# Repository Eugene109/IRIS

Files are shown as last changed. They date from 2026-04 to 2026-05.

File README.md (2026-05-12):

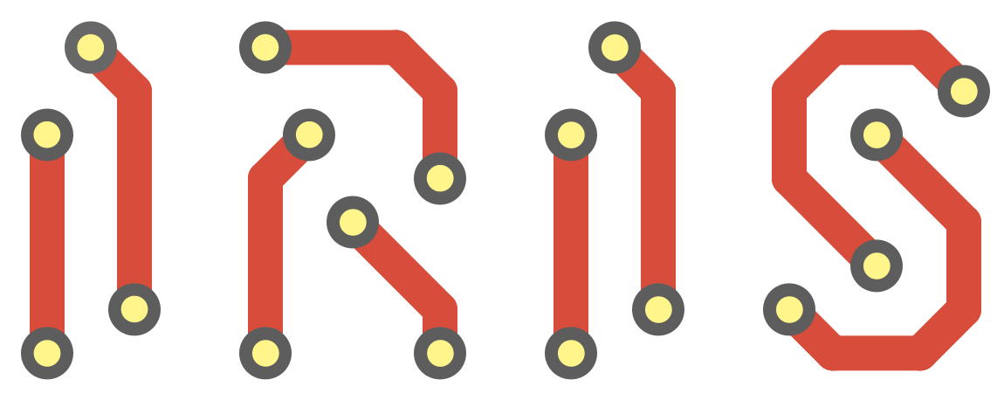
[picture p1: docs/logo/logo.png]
IRIS


> A low-cost quadcopter platform designed for autonomous swarm operations.



Photorealistic render from the back-right-top side of the drone

## Overview
IRIS is centered around a mass-manufacturable low-cost PCB, containing a flight controller and 4 ESCs. Designed with the idea of delivering Skittles autonomously, IRIS is built from the ground-up for autonomous operation in swarms. With a rich sensor set and high degree of customizability, IRIS represents an accessible, low-cost entry into the world of autonomous and swarm drone operations. I began this project because I found a lack of accessible drone designs that are for more than just 'fun FPV flying', and I wanted to be able to program a drone to do cool things. IRIS represents a rethinking of small drone design, believing that small drones can and should be autonomous and that everyone should be able to program a drone.
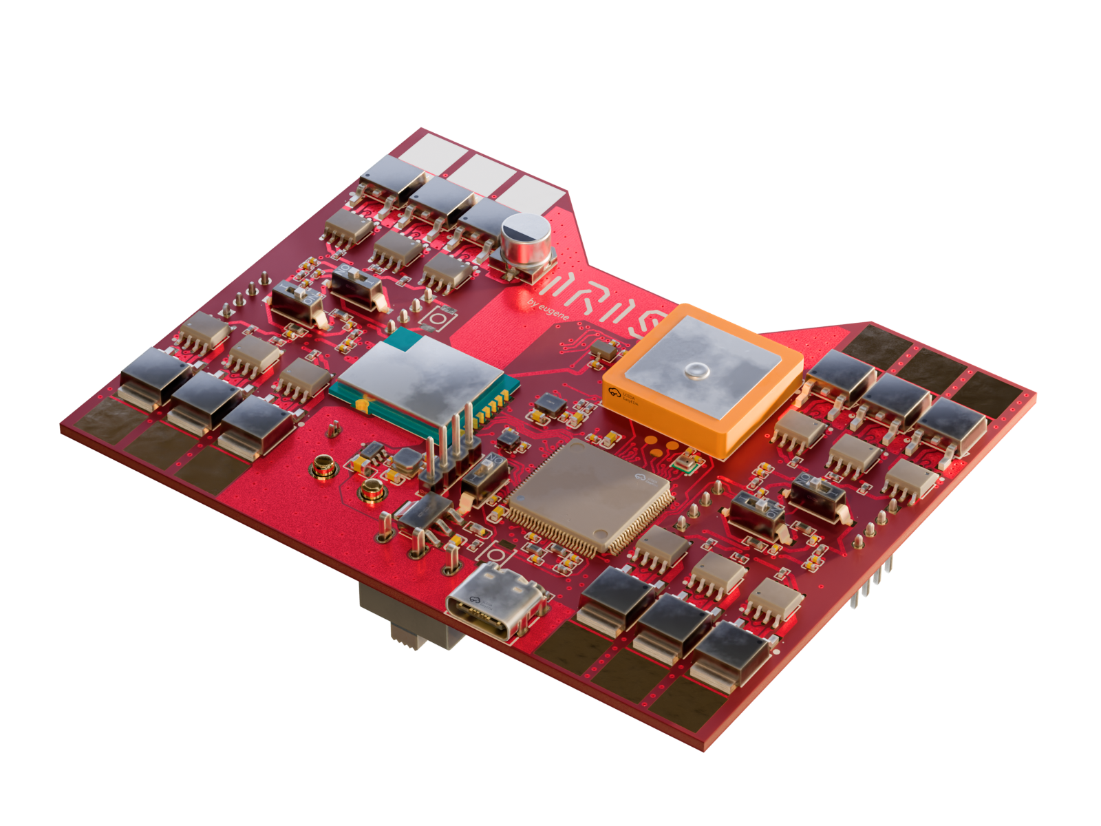
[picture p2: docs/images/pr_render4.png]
Photorealistic render of the front side of the PCB


## Features
 - STM32H743 MCU
 - IMU, Barometer, Magnetometer, GPS
 - Integrated 4-in-1 ESC with sensorless drive
 - OV2640 camera for computer vision
 - 2.4GHz Radio Transciever + nanoELRS header
 - 2S LiPo input, XT60 connector
 - 3D-printed frame

## Table of Contents
- [Design Features](#design-features)
  - [Flight Controller Design](#flight-controller-design)
  - [ESC Design](#esc-design)
  - [Frame Design](#frame-design)
- [Getting Started](#getting-started)
- [PCB Assembly](#pcb-assembly)
- [Bill of Materials](#bill-of-materials)
- [Drone Assembly](#drone-assembly)
- [Firmware](#firmware)
- [Roadmap](#roadmap)

## Hack Club Magazine Page
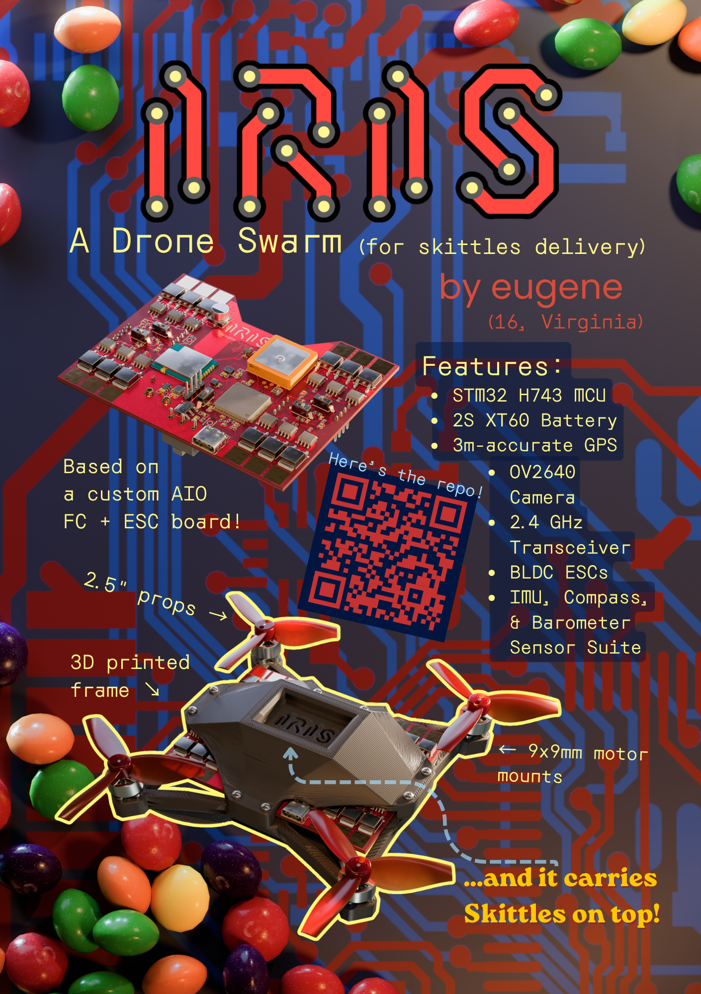
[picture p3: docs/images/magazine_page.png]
A5 magazine page


## Design Features

### Flight Controller Design
<p align="center">
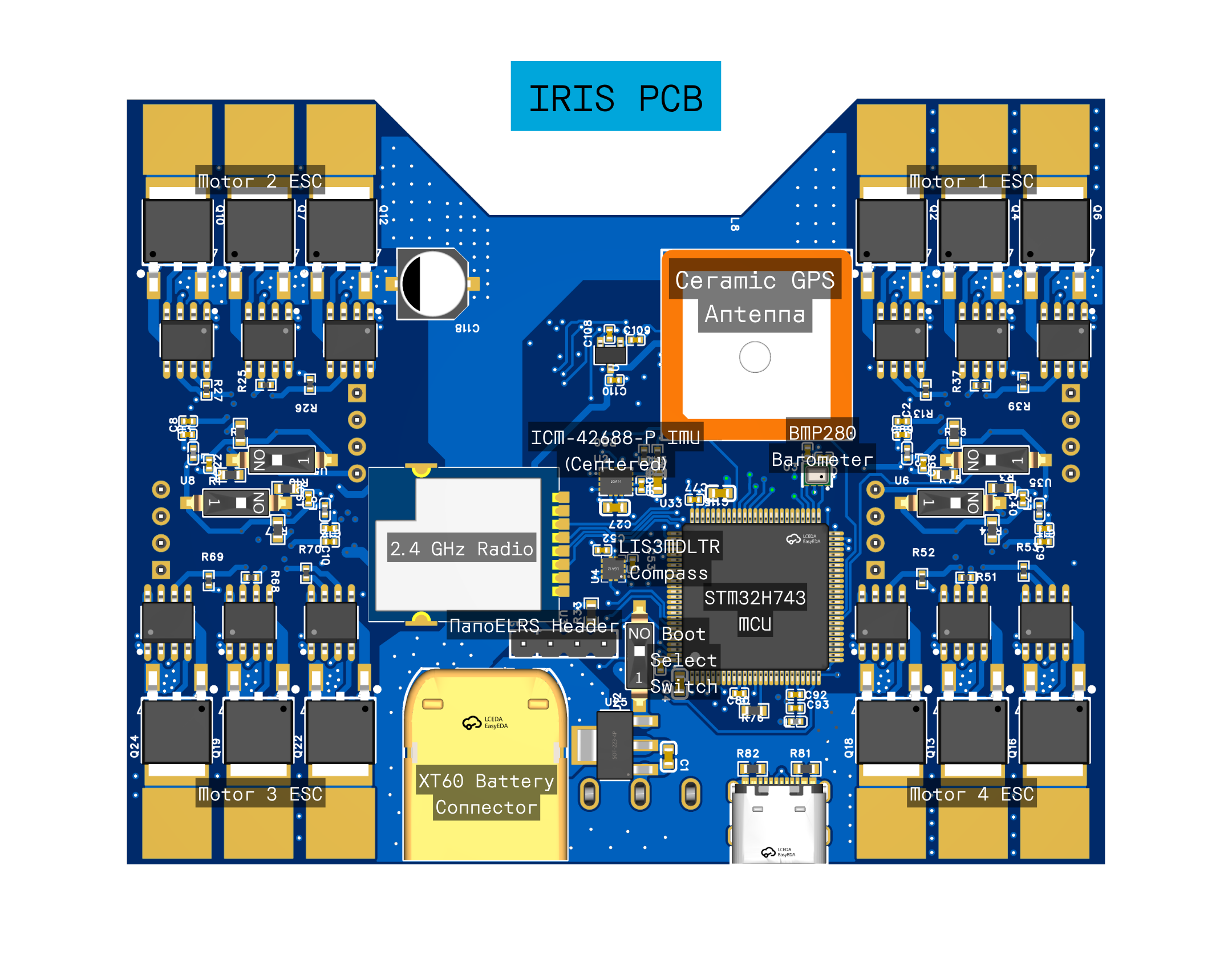
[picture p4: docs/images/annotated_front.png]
Annotated render of the front of the PCB
  
&nbsp; &nbsp; &nbsp; &nbsp;
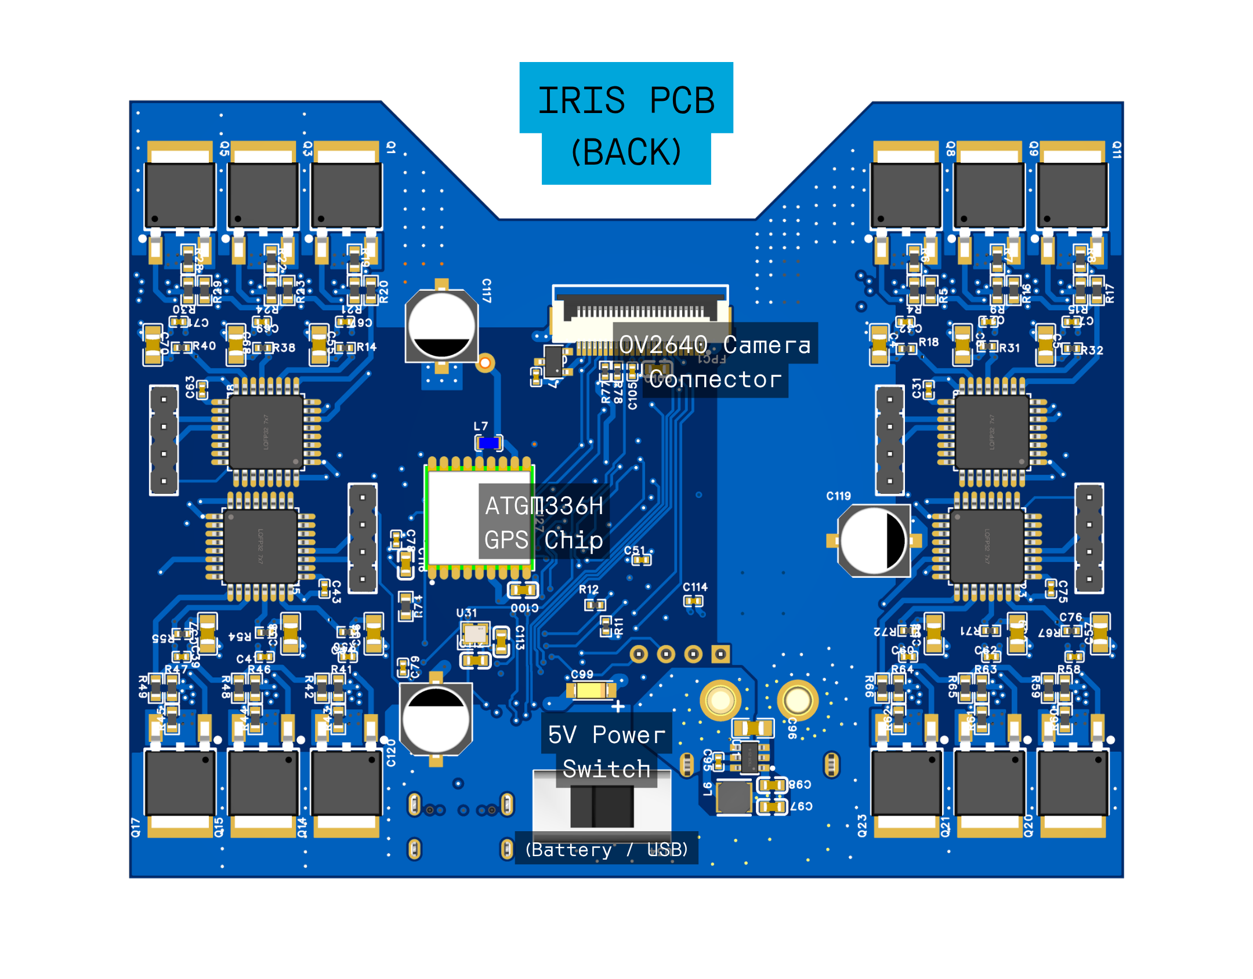
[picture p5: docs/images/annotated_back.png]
Annotated render of the back of the PCB
  
</p>

[Schematic](./pcb/schematics/Flight_Controller_Schematic.svg)

The PCB design features a 4-layer PCB stackup for lowered manufacturing costs, with a (nearly) continuous ground plane for reduced RF interference. The area under the MCU and core sensors also feature a continuous 3.3V power plane. The high voltage and current for the ESCs are routed on large copper pours on the bottom layer, with cross-layer connections connected by suture vias.

The total board dimensions are 3.650" by 2.856", a little larger than a credit card.

The main flight controller MCU is programmable over USB. The 4 ESC MCUs require a serial programmer, with ground, rx and tx exposed on header pins. All MCUs have a dedicated switch for a physical boot selector.

### ESC Design

[Schematic](./pcb/schematics/ESC_Schematics/Motor1_ESC_Schematic.svg)

The ESC design features an STM32F303K8T6 microcontroller, a very powerful MCU that enables accurate back-emf drive even for high kV motors. 

Loosely based off of this open-source design I found,
https://electronoobs.com/eng_arduino_tut91.php, the wiring diagram was very helpful to guide the general layout of my ESC. The control logic is loosely based off of the arduino code, though it had to be completely rewritten to interface with STM32 hardware (really all BLDC motor control logic is the same, but nice understandable code was helpful).

### Frame Design
The frame design merges swooping curves and sharp geometric angles in a retrofuturistic visual style. Inspired by the Theme Building at LAX, the frame arms are each constructed with 3 catenary curves, with the bottom arches merging together to form the cradle for the battery.

The bottom also features a -30º camera mount, which facilitates autonomous navigation, and turns into the perfect FPV mount when flown inverted.
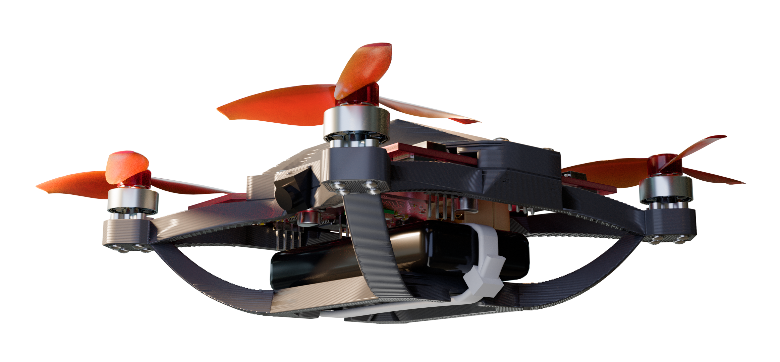
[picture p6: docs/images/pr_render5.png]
Photorealistic render from the back-left side of the drone


At the top of the frame, a little cradle with a minimalist IRIS logo debossed reserves space for a small collection of Skittles, easily dumped out by flipping the drone.

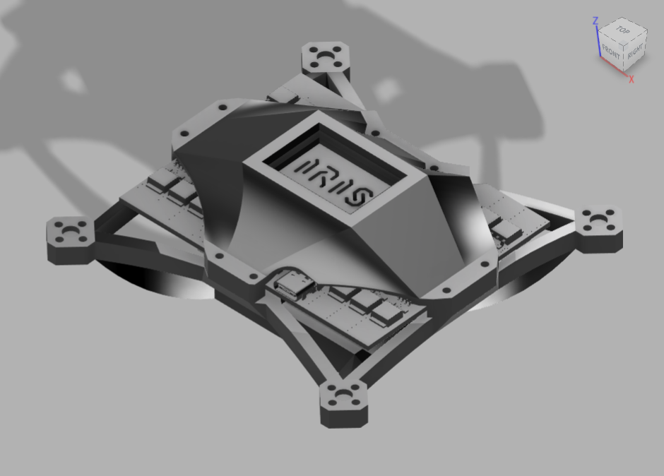
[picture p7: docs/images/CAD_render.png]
CAD render of the integrated frame + PCB


The drone frame is constructed in two pieces and held together by 8 M2 screws. The bottom half contains a battery mount and 4 9x9mm motor mounts, while the top half clamps the PCB down. The top cover shields the bulk of the PCB while leaving the high-current ESC MOSFET sections exposed for cooling, and is bolted down using 8 10mm long M2 screws and heat set inserts on the bottom half.

## Getting Started

### Prerequisites

- EasyEDA Pro (recommended)
- KiCAD 10.0 (broken DRC rules)
- Fusion 360
- Blender 5.0+ ([pcb2blender](https://github.com/30350n/pcb2blender) extension required for textures)

### For KiCAD Users:
This project was made in the free software EasyEDA Pro, and the design is native to that software. The PCB design has been converted to a KiCAD project for easier access to the design, but there may be some errors that have occurred during the import process, in particular trace clearances and zone fill rules.

> NOTE: The KiCAD imported project relies on 3D models and footprints from LCSC, which were imported using [easyeda2kicad.py](https://github.com/uPesy/easyeda2kicad.py).

### Repository Structure
All of the files for the flight controller + ESC board are contained in `pcb/`, with fabrication files in `pcb/fabrication/`. All fabrication files are to [JLCPCB](https://jlcpcb.com/) specifications. All part numbers are from [LCSC](https://www.lcsc.com/).

The frame CAD files can be found in the `frame/` directory, with (metric) STL and 3MF exports ready for 3D printing. The cover and bottom were designed in the same Fusion360 Part, and the IRIS_Assembly.f3z is the total assembly including parts I did not design.

All of the renders on the documentation were created using Blender 5.1, and render files can be found in `docs/render/`.

## PCB Assembly

### PCB Component Bill of Materials
[PCB Component BOM](./pcb/fabrication/BOM.md)

Total cost from LCSC: **$103.21**
[LCSC Quote](./pcb/fabrication/LCSC_BOM_export.xls)

### Assembly

The [PCB gerbers](./pcb/fabrication/gerbers.zip) can be manufactured by JLCPCB with the simple 4-layer PCBA economical service. Two-sided automated assembly is quite expensive however, so first prototypes will be assembled manually using solder stencils. PCB components can be ordered from LCSC using the [LCSC BOM](./pcb/fabrication/BOM_Board1_PCB1.xlsx).
> NOTE: The large copper pours are connected directly to a lot of the pads, manual soldering will require the use of a hot air rework station and powerful soldering iron

## Bill of Materials
> Note: the full list of components for the PCB was not included in this BOM to save space, the component BOM can be found [here](./pcb/fabrication/BOM.md)

| Part | Description | Link | Price |
| --- | --- | --- | ----- |
| FC+ESC | 4-layer PCB A Economic, HASL(leaded) finish, 2 stencils w/ framework | [JLCPCB](https://cart.jlcpcb.com/quote) (Please upload ./pcb/fabrication/gerbers.zip to order the PCB) | 29.23 |
| FC+ESC | IRIS PCB Components | [LCSC](https://www.lcsc.com/) (Please upload ./pcb/fabrication/BOM_Board1_PCB1.xlsx to order the components) | 103.21 |
| Battery | 1000 mAh 2S LiPo with XT60 connector| [Admiral](https://motionrc.com/products/admiral-1000mah-2s-7-4v-30c-lipo-battery-with-xt60-connector-epr10002x6) | 9.99 |
| Motors | 4x 8000 kV 1103 Brushless DC | [AliExpress](https://www.aliexpress.us/item/3256808118156099.html) | 23.99 |
| Propellers | Gemfan 2512 2.5Inch 3-Blade 1.5mm Hole Propeller - 4CW+4CCW | [Pyrodrone](https://pyrodrone.com/products/gemfan-2512-2-5inch-3-blade-1-5mm-2mm-hole-propeller-4cw-4ccw) | 4.99 |
| Camera | OV2640 with SCCB cable | [AliExpress](https://www.aliexpress.us/item/3256805331385102.html) | 4.20 |
| Heat-set inserts | M2x2.5mm, 3.5mm OD Knurled Brass Threaded Heat Set Inserts | [Rusty Bolt Shop](https://ebay.us/m/7A3cL3) | 1.70 |
| Frame screws | M2x10mm screws | [The Rusty Bolt Shop](https://ebay.us/m/wMPMiQ) | 2.02 |
| Motor mount screws | M2x8mm screws | [The Rusty Bolt Shop](https://ebay.us/m/UnEsMj) | 2.56 |
| Vibration dampening foam | 3M Double Coated Urethane Foam Tape 4056 | [Newegg](https://www.newegg.com/p/2VW-0006-00155?item=9SIA5D52U89288) | 14.99 |

Total: $196.88
(minus shipping)

## Drone Assembly
1. Print the frame in two sections
2. Attach heat-set inserts with a soldering iron on the base half of the frame.
3. Cut 4056 foam to shape and attach to the PCB contact areas on both sides of the frame.
4. Attach the OV2640 camera SCCB cable to the connector and attach 4056 foam to the back of the sensor.
5. Insert the assembled PCB between the two frame sections and bolt down all 8 M2x10mm screws.
6. Slot the camera sensor into its 30º mount and attach using 4056 foam.
7. Insert the battery into the cradle underneath the PCB, mount it with 4056 foam and fasten down with zip ties across the horizontal beams, inside of the grooves.
8. Attach brushless motors with M2x8mm screws.
9. Press-fit 2CCW and 2CW propellers onto the four brushless motors' 1.5mm shafts.
10. Flash the [Betaflight firmware](./firmware/betaflight/binaries/betaflight_2026.6.0-alpha_STM32H743_IRIS_H743.hex) using a USB-C cable.
11. Flash the [Zephyrus firmware](https://github.com/Eugene109/zephyrus/releases/latest) to all four ESCs using a serial programmer attached to the 4-pin headers.
11. Fly!

## Firmware
### Betaflight
This flight controller is capable of running Betaflight, and the configuration header for a Betaflight target can be found in `firmware/betaflight/`. The compiled binaries can be found in the same directory, and the `.hex` file is recommended. The source code can be found at the [Betaflight firmware repository](https://github.com/betaflight/betaflight), and the `config.h` file can be copied into the config directory to build it yourself.

The flight control software can be flashed using the USB-C port on the aft of the drone. Simply plug it in and use STMCubeProgrammer to flash it!

### Zephyrus
The ESCs run custom firmware, named Zephyrus. The binaries and source code is available at its [repository](https://github.com/Eugene109/zephyrus).

Zephyrus is currently capable of sensorless back-EMF drive, and runs on the STM32F303K8T6 MCU platform. The sensorless drive is powered by ADC zero-crossing detection synchronized with the PWM output to the MOSFET drivers. The choice to use software detection of zero-crossing over hardware comparators was for the increased flexibility as the firmware matures, enabling more interesting control systems than just zero-crossing alone.

The ESCs are a bit harder to flash, though they should require only a single flashing when the firmware is tuned. Connect a serial programmer (FTDI, hijack an Arduino, etc) to the RX, TX, and GND pins and flash the MCU using the ROM bootloader. To switch the MCU to the built-in bootloader to program, simply flip the boot selector switch and press the reset button.

## Roadmap

- [X] PCB designed
- [X] Case designed
- [ ] PCB assembled
- [ ] Prototype assembled
- [ ] Prototype tested
- [ ] Firmware finalized
- [ ] PCB mass-produced

## License

Everything is [GNU GPL-3.0](LICENSE)

zephyrus firmware is licensed under MIT, check its [repo](https://github.com/Eugene109/zephyrus) for more information.

> **Trademark Notice:** Skittles® is a registered trademark of Mars, Inc. This project is not affiliated with, or sponsored by Mars, Inc. References to Skittles and any associated imagery are for descriptive purposes only.

### Attribution
1103 BLDC motor 3D model used in Fusion Assembly is from [GrabCAD](https://grabcad.com/library/geprc-gr1103-1) by [Dang Ngoc Duy](https://grabcad.com/dang.ngoc.duy-1)

2.5" propeller 3D model used in Fusion Assembly is from [GrabCAD](https://www.thingiverse.com/thing:6901068) by [Buddhas_Priest](https://www.thingiverse.com/Buddhas_Priest)

rostock_laage_airport_4k.exr is CC0 from PolyHaven, credit to Greg Zaal

Inspiration was taken from [Electronoobs's ESC design], informing the framework for a standard ESC architecture.

None of the PCB 3D models are my own work, they come from LCSC's libraries.

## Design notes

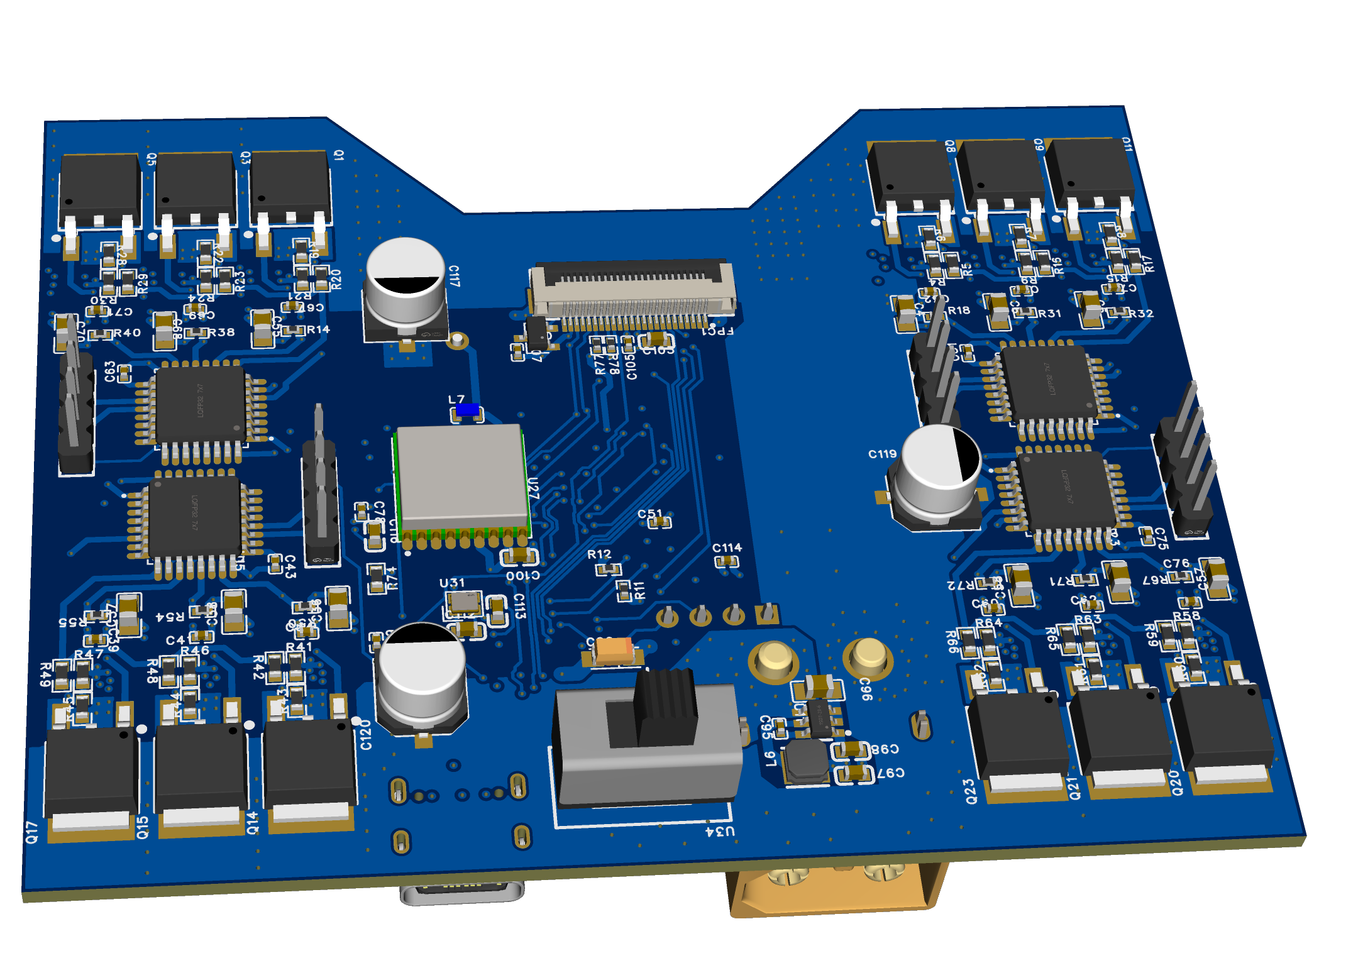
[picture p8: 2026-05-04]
docs/images/PCB_Back_RENDER.png

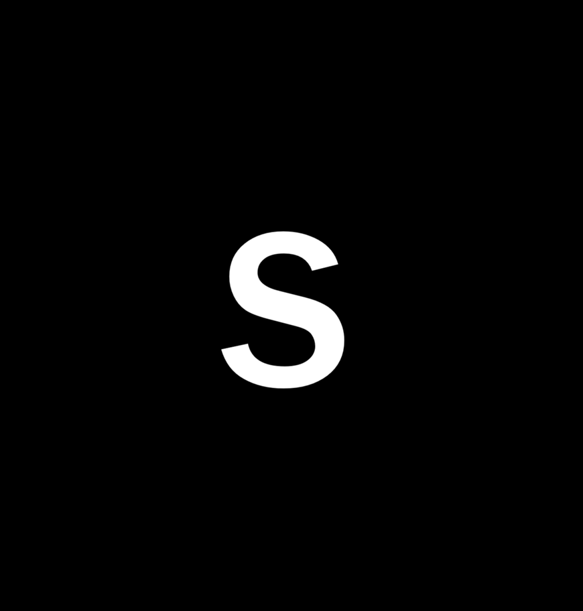
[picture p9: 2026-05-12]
docs/render/s.png

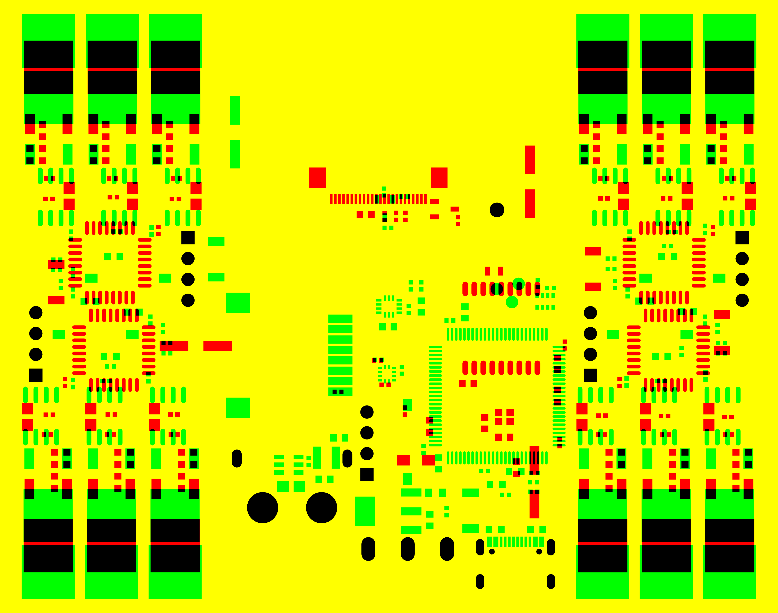
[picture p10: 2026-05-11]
docs/render/textures/IRIS_PCB_model_Mask.png

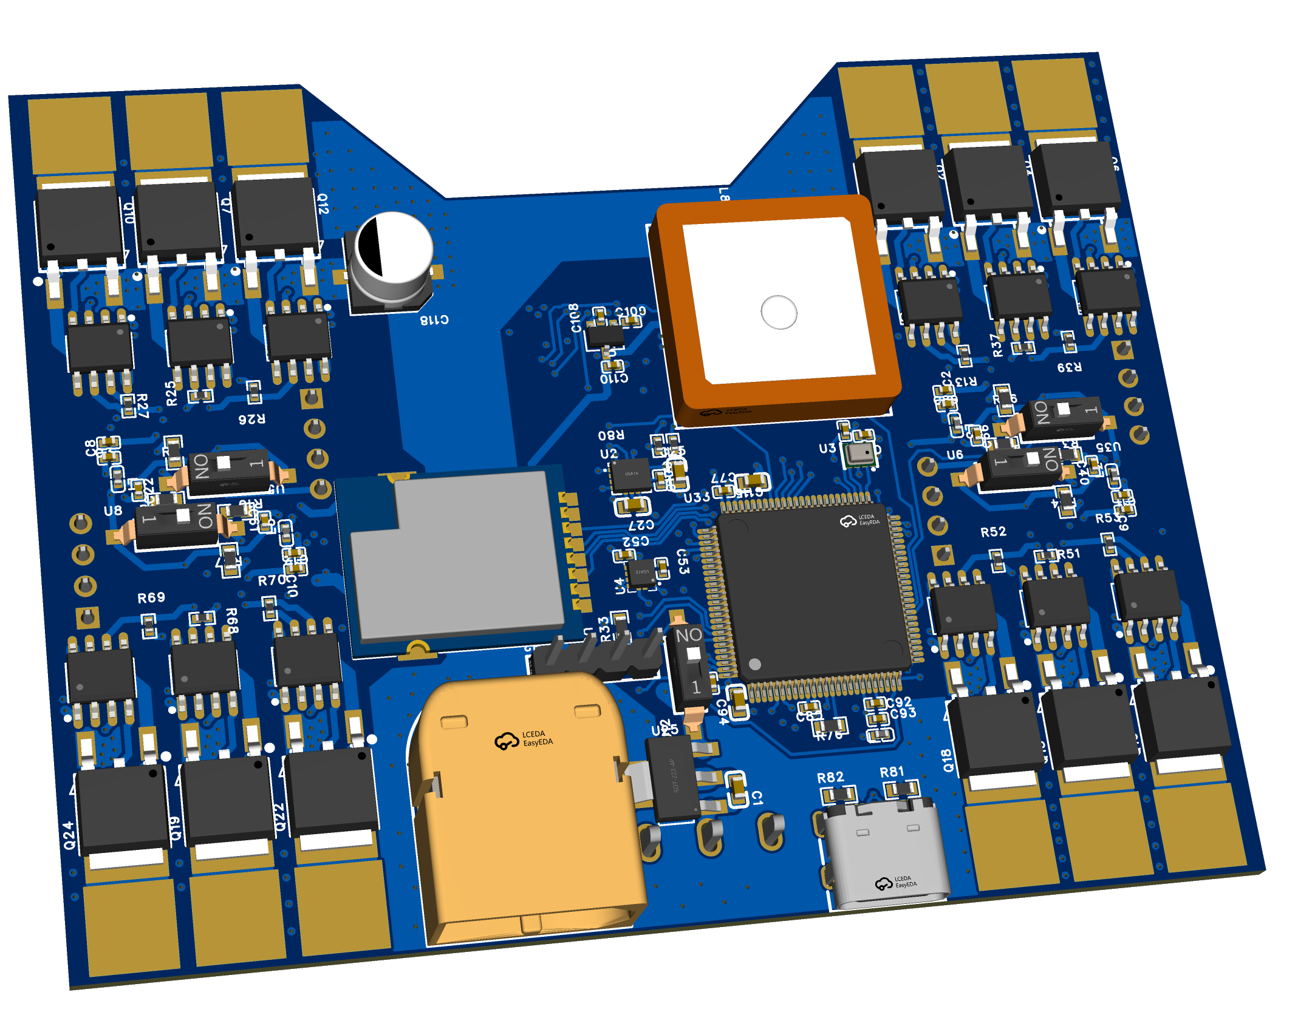
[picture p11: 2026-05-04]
docs/images/PCB_Front_RENDER.png

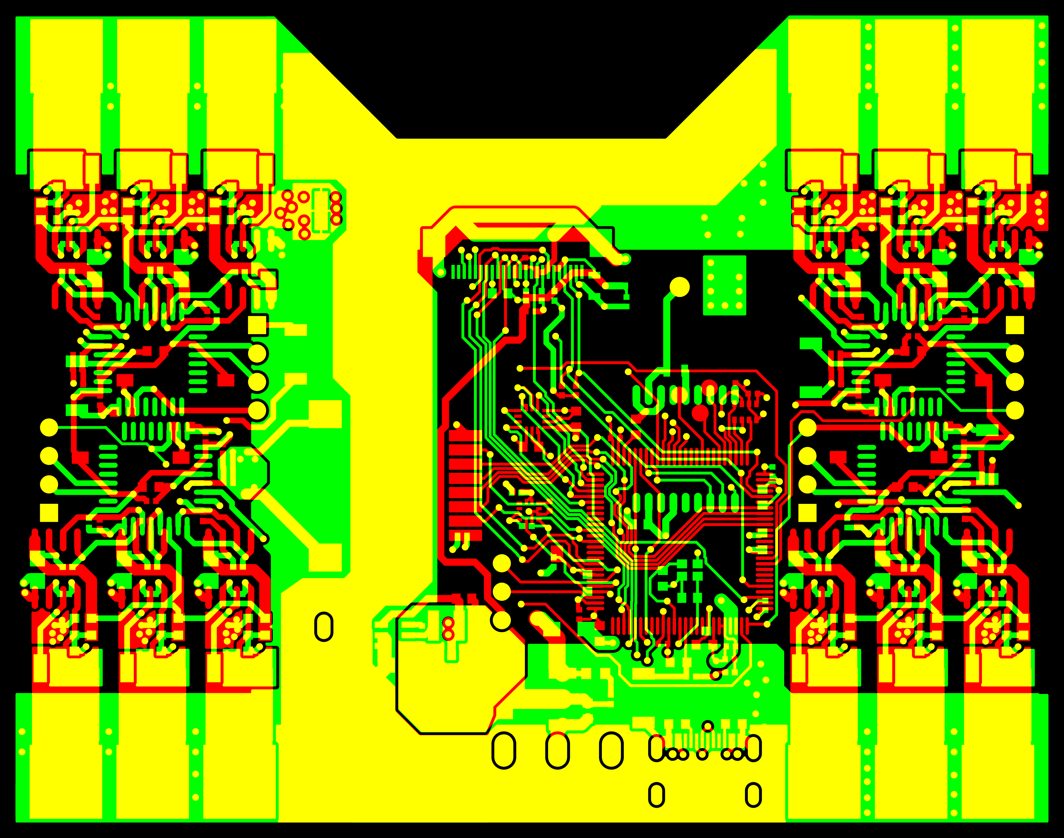
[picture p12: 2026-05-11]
docs/render/textures/IRIS_PCB_model_Cu.png

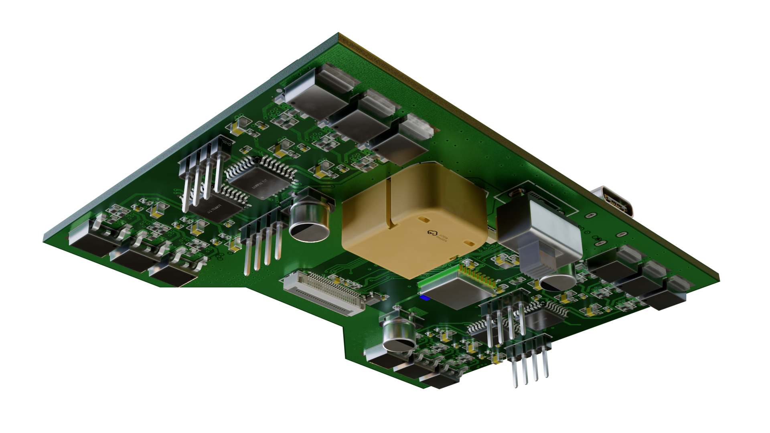
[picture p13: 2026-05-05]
docs/images/pr_render2.png

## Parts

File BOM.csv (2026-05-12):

Quantity | Part | Description | Source | Link | Price
1 | FC+ESC | 4-layer PCB A Economic HASL(leaded) finish 2 stencils w/ framework | JLCPCB | N/A: Please upload pcb/fabrication/gerbers.zip to https://www.jlcpcb.com/ to order | 29.23
1 | FC+ESC | IRIS PCB Components | LCSC | Please upload pcb/fabrication/BOM_Board1_PCB1.xlsx to https://www.lcsc.com/; alternatively see pcb/fabrication/BOM.md for LCSC links | 103.21
1 | Battery | 1000 mAh 2S LiPo with XT60 connector | Admiral | https://motionrc.com/products/admiral-1000mah-2s-7-4v-30c-lipo-battery-with-xt60-connector-epr10002x6 | 9.99
1 | Motors | 4x 8000 kV 1103 Brushless DC | AliExpress | https://www.aliexpress.us/item/3256808118156099.html | 23.99
1 | Propellers | Gemfan 2512 2.5Inch 3-Blade 1.5mm Hole Propeller - 4CW+4CCW | Pyrodrone | https://pyrodrone.com/products/gemfan-2512-2-5inch-3-blade-1-5mm-2mm-hole-propeller-4cw-4ccw | 4.99
1 | Camera | OV2640 with SCCB cable | AliExpress | https://www.aliexpress.us/item/3256805331385102.html | 4.20
1 | Heat-set inserts | M2x2.5mm 3.5mm OD Knurled Brass Threaded Heat Set Inserts | Rusty Bolt Shop | https://ebay.us/m/7A3cL3 | 1.70
1 | Frame screws | M2x10mm screws | The Rusty Bolt Shop | https://ebay.us/m/wMPMiQ | 2.02
1 | Motor mount screws | M2x8mm screws | The Rusty Bolt Shop | https://ebay.us/m/UnEsMj | 2.56
1 | Vibration dampening foam | 3M Double Coated Urethane Foam Tape 4056 | Newegg | https://www.newegg.com/p/2VW-0006-00155?item=9SIA5D52U89288 | 14.99

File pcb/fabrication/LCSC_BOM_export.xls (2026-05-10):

BOM_Board1_PCB1.xlsx |  |  |  |  |  |  |  |  |  | LCSC BOM Quotation
 |  |  |  |  |  |  |  |  |  | BOM Date Created：11/05/26 04:00:47 |  |  |  | BOM Export Date: 11/05/26 04:02:04 |  |  |  | The matching result is a real-time query result, availability and prices may fluctuate. Backorder items are estimated prices for your reference, please submit "Create Quote" to get the real price. All information is provided "as is" and is subject to change without notice. Any use made of the information provided is without recourse to LCSC and at the user's risk.
 |  |  |  |  |  |  |  |  |  | EST TOTAL :$103.21 |  |  |  | Website：https://www.lcsc.com/bom | https://www.lcsc.com/bom | https://www.lcsc.com/bom | https://www.lcsc.com/bom
Uploaded data |  |  |  |  |  |  |  |  |  | LCSC Matching Results
LCSC# | Mfr. | Mrf# | Description | Package | Value | Customer Part Number | Quantity | Target Price(USD) | Target Lead Time(Business Days) | Mrf# | Mfr. | Order Qty. | Unit Price(USD) | Ext.Price(USD) | LCSC# | Package | Min | Mult | SPQ | Availability | Stock Status | Customer Notes | Description | Matched status | Product Link
C19702 | SAMSUNG(三星) | CL10A106KP8NNNC | 10uF | C0603 |  | C1,C100 | 2 |  |  | CL10A106KP8NNNC | Samsung Electro-Mechanics | 50 | 0.0103 | 0.52 | C19702 | 0603 | 50 | 50 | 4000 | 0 | Backordered |  | 10uF ±10% 10V Ceramic Capacitor X5R 0603 | Exact Matches | https://www.lcsc.com/product-detail/C19702.html
C29266 | SAMSUNG(三星) | CL05A105KO5NNNC | 1uF | C0402 |  | C2,C8,C9,C10,C51,C93,C107,C108,C109,C110 | 10 |  |  | CL05A105KO5NNNC | Samsung Electro-Mechanics | 100 | 0.0030 | 0.30 | C29266 | 0402 | 100 | 100 | 10000 | 2823500 | In Stock |  | 1uF ±10% 16V Ceramic Capacitor X5R 0402 | Exact Matches | https://www.lcsc.com/product-detail/C29266.html
C53084459 | TORCH(火炬) | CC0402X7R25V104KN | 100nF | C0402 |  | C3,C7,C11,C12,C13,C14,C15,C16,C22,C24,C28,C29,C31,C32,C39,C40,C4 | 43 |  |  | CC0402X7R25V104KN | TORCH | 100 | 0.0023 | 0.23 | C53084459 | 0402 | 100 | 100 | 10000 | 49200 | In Stock |  | 100nF X7R ±10% 25V 0402 Ceramic Capacitors RoHS | Exact Matches | https://www.lcsc.com/product-detail/C53084459.html
C602037 | SAMSUNG(三星) | CL21A226MAYNNNE | 22uF | C0805 |  | C4,C5,C6,C36,C37,C38,C55,C57,C58,C59,C68,C70 | 12 |  |  | CL21A226MAYNNNE | Samsung Electro-Mechanics | 20 | 0.0431 | 0.86 | C602037 | 0805 | 10 | 10 | 2000 | 1569470 | In Stock |  | 22uF ±20% 25V Ceramic Capacitor X5R 0805 | Exact Matches | https://www.lcsc.com/product-detail/C602037.html
C23630 | SAMSUNG(三星) | CL10A225KO8NNNC | 2.2uF | C0603 |  | C25,C115,C116 | 3 |  |  | CL10A225KO8NNNC | Samsung Electro-Mechanics | 50 | 0.0068 | 0.34 | C23630 | 0603 | 50 | 50 | 4000 | 1071250 | In Stock |  | 2.2uF ±10% 16V Ceramic Capacitor X5R 0603 | Exact Matches | https://www.lcsc.com/product-detail/C23630.html
C100042 | YAGEO(国巨) | CC0603KRX7R9BB103 | 10nF | C0603 |  | C27 | 1 |  |  | CC0603KRX7R9BB103 | YAGEO | 100 | 0.0026 | 0.26 | C100042 | 0603 | 100 | 100 | 4000 | 4009100 | In Stock |  | 10nF ±10% 50V Ceramic Capacitor X7R 0603 | Exact Matches | https://www.lcsc.com/product-detail/C100042.html
C19666 | SAMSUNG(三星) | CL10A475KO8NNNC | 4.7uF | C0603 |  | C94 | 1 |  |  | CL10A475KO8NNNC | Samsung Electro-Mechanics | 10 | 0.0111 | 0.11 | C19666 | 0603 | 10 | 10 | 4000 | 2586850 | In Stock |  | 4.7uF ±10% 16V Ceramic Capacitor X5R 0603 | Exact Matches | https://www.lcsc.com/product-detail/C19666.html
C95841 | SAMSUNG(三星) | CL21B106KOQNNNE | 10uF | C0805 |  | C96 | 1 |  |  | CL21B106KOQNNNE | Samsung Electro-Mechanics | 10 | 0.0301 | 0.30 | C95841 | 0805 | 10 | 10 | 2000 | 535120 | In Stock |  | 10uF ±10% 16V Ceramic Capacitor X7R 0805 | Exact Matches | https://www.lcsc.com/product-detail/C95841.html
C86295 | SAMSUNG(三星) | CL10A226MP8NUNE | 22uF | C0603 |  | C97,C98 | 2 |  |  | CL10A226MP8NUNE | Samsung Electro-Mechanics | 10 | 0.0157 | 0.16 | C86295 | 0603 | 10 | 10 | 3000 | 55500 | In Stock |  | 22uF ±20% 10V Ceramic Capacitor X5R 0603 | Exact Matches | https://www.lcsc.com/product-detail/C86295.html
C7171 | Kyocera AVX | TAJA106K016RNJ | 10uF | CAP-SMD_L3.2-W1.6-RD-C7171 |  | C99 | 1 |  |  | TAJA106K016RNJ | Kyocera AVX | 2 | 0.1292 | 0.26 | C7171 | CASE-A-3216-18(mm) | 2 | 2 | 2000 | 499488 | In Stock |  | 10uF ±10% 16V Tantalum Capacitors 3Ω@100kHz CASE-A-3216-18(mm) | Exact Matches | https://www.lcsc.com/product-detail/C7171.html
C1644 | SAMSUNG(三星) | CL10C150JB8NNNC | 15pF | C0603 |  | C103 | 1 |  |  | CL10C150JB8NNNC | Samsung Electro-Mechanics | 100 | 0.0060 | 0.60 | C1644 | 0603 | 100 | 100 | 4000 | 814200 | In Stock |  | 15pF ±5% 50V Ceramic Capacitor C0G 0603 | Exact Matches | https://www.lcsc.com/product-detail/C1644.html
C106245 | YAGEO(国巨) | CC0603JRNPO9BN100 | 10pF | C0603 |  | C112,C113 | 2 |  |  | CC0603JRNPO9BN100 | YAGEO | 100 | 0.0028 | 0.28 | C106245 | 0603 | 100 | 100 | 4000 | 6399600 | In Stock |  | 10pF ±5% 50V Ceramic Capacitor NP0 0603 | Exact Matches | https://www.lcsc.com/product-detail/C106245.html
C47023104 | JIERR(捷而瑞) | RVT16V330M6X8 | 330uF | CAP-SMD_BD6.3-L6.6-W6.6-LS7.2-FD_3 |  | C117,C118,C119,C120 | 4 |  |  | RVT16V330M6X8 | JIERR | 10 | 0.0508 | 0.51 | C47023104 | SMD,D6.3xL7.7mm | 10 | 10 | 1000 | 48060 | In Stock |  | 330uF ±20% 16V Aluminum Electrolytic Capacitors 2000hrs@105℃ | Exact Matches | https://www.lcsc.com/product-detail/C47023104.html
C98732 | AMASS(艾迈斯) | XT60PW-M |  | CONN-TH_XT60PW-M |  | CN1 | 1 |  |  | XT60PW-M | Changzhou Amass Elec | 1 | 0.5199 | 0.52 | C98732 | - | 1 | 1 | 250 | 22214 | In Stock |  | Horizontal plug Power Connectors RoHS | Exact Matches | https://www.lcsc.com/product-detail/C98732.html
C2856805 | XUNPU(讯普) | FPC-05F-24PH20 |  | FPC-SMD_24P-P0.50_FPC-05F-24PH20 |  | FPC1 | 1 |  |  | FPC-05F-24PH20 | XUNPU | 5 | 0.0958 | 0.48 | C2856805 | SMD,P=0.5mm,Surface Mount,Right Angle | 5 | 5 | 2000 | 55720 | In Stock |  | FFC/FPC Connector 24 Position 0.5mm Pitch Bottom Contact Surface Mount, Right Angle -25℃~+85℃ | Exact Matches | https://www.lcsc.com/product-detail/C2856805.html
C52016392 | hanxia(韩下) | HX PH254-01-04-Z-L11.5 straight pin header |  | HDR-TH_4P-HX-PH254-01-04-Z-L11.5 |  | H1,H2,H3,H4,H5 | 5 |  |  | HX PH254-01-04-Z-L11.5 straight pin header | hanxia | 20 | 0.0305 | 0.61 | C52016392 | Through Hole,P=2.54mm | 20 | 20 | 2000 | 36120 | In Stock |  | Pin Header 1 2.5mm 6mm -40℃~+105℃ 3mm 4P 2.54mm 3A 1kV 1x4P Through Hole,P=2.54mm Headers, Male Pins RoHS | Exact Matches | https://www.lcsc.com/product-detail/C52016392.html
C76891 | muRata(村田) | BLM15PD121SN1D |  | L0402 |  | L1,L2,L3,L4,L5 | 5 |  |  | BLM15PD121SN1D | muRata | 100 | 0.0094 | 0.94 | C76891 | 0402 | 100 | 100 | 10000 | 411100 | In Stock |  | 120Ω@100MHz 1 Line Ferrite Bead 0402 1.3A 90mΩ | Exact Matches | https://www.lcsc.com/product-detail/C76891.html
C7427089 | APV(爱普微) | ANR3015T4R7M | 4.7uH | IND-SMD_L3.0-W3.0-1 |  | L6 | 1 |  |  | ANR3015T4R7M | APV | 20 | 0.0369 | 0.74 | C7427089 | SMD,3x3mm | 20 | 20 | 2000 | 189740 | In Stock |  | 1.3A 4.7uH ±20% 1.4A Magnetic Shielded Inductor SMD,3x3mm Fixed Inductors RoHS | Exact Matches | https://www.lcsc.com/product-detail/C7427089.html
C6807998 | APV(爱普微) | AHW1608C-47NJTF | 47nH | IND-SMD_L1.8-W1.0 |  | L7 | 1 |  |  | AHW1608C-47NJTF | APV | 20 | 0.0401 | 0.80 | C6807998 | 0603 | 20 | 20 | 4000 | 12820 | In Stock |  | 600mA 47nH ±5% 280mΩ Wire-wound chip inductor 0603 Fixed Inductors RoHS | Exact Matches | https://www.lcsc.com/product-detail/C6807998.html
C784395 | BAT WIRELESS(蝙蝠无线) | BWGNSCNX18-18W4 |  | ANT-TH_L18.0-W18.0_C9900026472 |  | L8 | 1 |  |  | BWGNSCNX18-18W4 | BAT WIRELESS | 1 | 0.6977 | 0.70 | C784395 | Through Hole,18x18mm | 1 | 1 | 100 | 2140 | In Stock |  | RF ANTENNA Ceramic Through Hole,18x18mm | Exact Matches | https://www.lcsc.com/product-detail/C784395.html
C19268133 | TECH PUBLIC(台舟) | IRLR7843TRPBF |  | TO-252-3_L6.6-W6.1-P4.57-LS9.9-BR-CW |  | Q1,Q2,Q3,Q4,Q5,Q6,Q7,Q8,Q9,Q10,Q11,Q12,Q13,Q14,Q15,Q16,Q17,Q18,Q | 24 |  |  | IRLR7843TRPBF | TECH PUBLIC | 24 | 0.3429 | 8.23 | C19268133 | TO-252-3L | 1 | 1 | 2500 | 4844 | In Stock |  | 30V 150A 90W Surface Mount TO-252-3L | Exact Matches | https://www.lcsc.com/product-detail/C19268133.html
C98220 | YAGEO(国巨) | RC0603FR-0710KL | 10kΩ | R0603 |  | R1,R2,R3,R4,R9,R10,R15,R21,R24,R30,R33,R34,R36,R41,R46,R47,R57,R | 24 |  |  | RC0603FR-0710KL | YAGEO | 100 | 0.0015 | 0.15 | C98220 | 0603 | 100 | 100 | 5000 | 0 | Backordered |  | 100mW 10kΩ 75V Thick Film Resistor ±100ppm/℃ ±1% 0603 Chip Resistor - Surface Mount RoHS | Exact Matches | https://www.lcsc.com/product-detail/C98220.html
C2907028 | FOJAN(富捷) | FRC0603F3302TS | 33kΩ | R0603 |  | R5,R6,R7,R8,R16,R17,R19,R20,R22,R23,R28,R29,R42,R43,R44,R45,R48, | 25 |  |  | FRC0603F3302TS | FOJAN | 100 | 0.0010 | 0.10 | C2907028 | 0603 | 100 | 100 | 5000 | 1838100 | In Stock |  | 33kΩ ±1% 100mW 0603 Thick Film Resistor | Exact Matches | https://www.lcsc.com/product-detail/C2907028.html
C2906920 | FOJAN(富捷) | FRC0402J222 TS | 2.2kΩ | R0402 |  | R11,R12,R79,R80 | 4 |  |  | FRC0402J222 TS | FOJAN | 100 | 0.0006 | 0.06 | C2906920 | 0402 | 100 | 100 | 10000 | 1410900 | In Stock |  | 2.2kΩ ±5% 62.5mW 0402 Thick Film Resistor | Exact Matches | https://www.lcsc.com/product-detail/C2906920.html
C163475 | YAGEO(国巨) | RC0402FR-07270KL | 270kΩ | R0402 |  | R13,R14,R37,R38,R39,R40,R50,R51,R52,R53,R54,R55,R67,R68,R69,R70, | 18 |  |  | RC0402FR-07270KL | YAGEO | 100 | 0.0009 | 0.09 | C163475 | 0402 | 100 | 100 | 10000 | 327800 | In Stock |  | 62.5mW 270kΩ 50V Thick Film Resistor ±100ppm/℃ ±1% 0402 Chip Resistor - Surface Mount RoHS | Exact Matches | https://www.lcsc.com/product-detail/C163475.html
C60491 | YAGEO(国巨) | RC0402FR-07100KL | 100kΩ | R0402 |  | R18,R25,R26,R27,R31,R32 | 6 |  |  | RC0402FR-07100KL | YAGEO | 100 | 0.0008 | 0.08 | C60491 | 0402 | 100 | 100 | 10000 | 4226400 | In Stock |  | 100kΩ 62.5mW 50V Thick Film Resistor ±100ppm/℃ ±1% 0402 Chip Resistor - Surface Mount RoHS | Exact Matches | https://www.lcsc.com/product-detail/C60491.html
C106235 | YAGEO(国巨) | RC0402FR-071KL | 1kΩ | R0402 |  | R77 | 1 |  |  | RC0402FR-071KL | YAGEO | 100 | 0.0008 | 0.08 | C106235 | 0402 | 100 | 100 | 10000 | 582500 | In Stock |  | 1kΩ 62.5mW 50V Thick Film Resistor ±100ppm/℃ ±1% 0402 Chip Resistor - Surface Mount RoHS | Exact Matches | https://www.lcsc.com/product-detail/C106235.html
C105871 | YAGEO(国巨) | RC0402FR-074K7L | 4.7kΩ | R0402 |  | R78 | 1 |  |  | RC0402FR-074K7L | YAGEO | 100 | 0.0008 | 0.08 | C105871 | 0402 | 100 | 100 | 10000 | 3361800 | In Stock |  | 4.7kΩ ±1% 62.5mW 0402 Thick Film Resistor | Exact Matches | https://www.lcsc.com/product-detail/C105871.html
C2907044 | FOJAN(富捷) | FRC0603F5101TS | 5.1kΩ | R0603 |  | R81,R82 | 2 |  |  | FRC0603F5101TS | FOJAN | 100 | 0.0012 | 0.12 | C2907044 | 0603 | 100 | 100 | 5000 | 8552800 | In Stock |  | 5.1kΩ ±1% 100mW 0603 Thick Film Resistor | Exact Matches | https://www.lcsc.com/product-detail/C2907044.html
C2909315 | FOJAN(富捷) | FRC0402F1200TS | 120Ω | R0402 |  | R83 | 1 |  |  | FRC0402F1200TS | FOJAN | 100 | 0.0006 | 0.06 | C2909315 | 0402 | 100 | 100 | 10000 | 770100 | In Stock |  | 120Ω ±1% 62.5mW 0402 Thick Film Resistor | Exact Matches | https://www.lcsc.com/product-detail/C2909315.html
C53447012 | LXWCONN(连兴旺电子) | LXW-4X3X2-SMD |  | SW-SMD_L3.9-W3.0-LS5.0 |  | SW1,SW2,SW3,SW4,SW5 | 5 |  |  | LXW-4X3X2-SMD | LXWCONN | 20 | 0.0315 | 0.63 | C53447012 | SMD | 20 | 20 | 4000 | 3480 | In Stock |  | 12V Without Bracket 3mm Round Button SPST-NO 3.9mm 50mA SMD Tactile Switches RoHS | Exact Matches | https://www.lcsc.com/product-detail/C53447012.html
C628051 | MICROCHIP(美国微芯) | MIC4605-1YM-TR |  | SOIC-8_L4.9-W3.9-P1.27-LS6.0-BL |  | U1,U7,U10,U13,U14,U16,U17,U19,U20,U21,U22,U24 | 12 |  |  | MIC4605-1YM-TR | MICROCHIP | 12 | 1.1185 | 13.42 | C628051 | SOIC-8 | 1 | 1 | 2500 | 44 | In Stock |  | 5.5V~16V 1A 1A SOIC-8 Gate Drivers RoHS | Exact Matches | https://www.lcsc.com/product-detail/C628051.html
C1850418 | TDK InvenSense(应美盛) | ICM-42688-P |  | LGA-14_L3.0-W2.5-P0.50-TL |  | U2 | 1 |  |  | ICM-42688-P | TDK InvenSense | 1 | 12.8818 | 12.88 | C1850418 | LGA-14(2.5x3) | 1 | 1 | 5000 | 4499 | In Stock |  | LGA-14(2.5x3) IMUs (Inertial Measurement Units) RoHS | Exact Matches | https://www.lcsc.com/product-detail/C1850418.html
C83291 | Bosch(博世) | BMP280 |  | LGA-8_L2.5-W2.0-P0.65_AMP6127 |  | U3 | 1 |  |  | BMP280 | Bosch | 1 | 6.0318 | 6.03 | C83291 | LGA-8(2x2.5) | 1 | 1 | 10000 | 6487 | In Stock |  | 30Kpa~1.1bar LGA-8(2x2.5) Pressure Sensors, Transducers RoHS | Exact Matches | https://www.lcsc.com/product-detail/C83291.html
C478483 | ST(意法半导体) | LIS3MDLTR |  | LGA-12_L2.0-W2.0-P0.50-BL |  | U4 | 1 |  |  | LIS3MDLTR | ST | 1 | 5.0410 | 5.04 | C478483 | LGA-12(2x2) | 1 | 1 | 8000 | 16455 | In Stock |  | LGA-12(2x2) Linear, Compass (ICs) RoHS | Exact Matches | https://www.lcsc.com/product-detail/C478483.html
C7421519 | SHOU HAN(首韩) | 2.54-1P TPGT |  | SW-SMD_2P-L6.2-W2.5-LS9.4 |  | U5,U6,U8,U12,U35 | 5 |  |  | 2.54-1P TPGT | SHOU HAN | 5 | 0.4612 | 2.31 | C7421519 | SMD,P=2.54mm | 1 | 1 | 1000 | 16472 | In Stock |  | Dip Switch SPST 1 Position Surface Mount Slide, Rocked 25mA 24V | Exact Matches | https://www.lcsc.com/product-detail/C7421519.html
C118318 | ST(意法半导体) | STM32F303K8T6 |  | LQFP-32_L7.0-W7.0-P0.80-LS9.0-BL |  | U9,U15,U18 | 3 |  |  | STM32F303K8T6 | ST | 3 | 7.4532 | 22.36 | C118318 | LQFP-32(7x7) | 1 | 1 | 250 | 54 | In Stock |  | ARM Cortex-M4 32 Bit 72MHz 25 LQFP-32(7x7) Microcontrollers RoHS | Exact Matches | https://www.lcsc.com/product-detail/C118318.html
C2071056 | DIODES(美台) | AP63205WU-7 |  | TSOT-23-6_L2.9-W1.6-P0.95-LS2.8-BL |  | U11 | 1 |  |  | AP63205WU-7 | DIODES | 1 | 0.4719 | 0.47 | C2071056 | TSOT-23-6 | 1 | 1 | 3000 | 22427 | In Stock |  | 1.1MHz Step-down type Fixed 2A 5V TSOT-23-6 Voltage Regulators - DC DC Switching Regulators RoHS | Exact Matches | https://www.lcsc.com/product-detail/C2071056.html
C2054944 | ST(意法半导体) | STM32F051K8T6TR |  | LQFP-32_L7.0-W7.0-P0.80-LS9.0-BL |  | U23 | 1 |  |  | STM32F051K8T6TR | ST | 1 | 1.5789 | 1.58 | C2054944 | LQFP-32(7x7) | 1 | 1 | 2400 | 871 | In Stock |  | ARM Cortex-M0 32 Bit 48MHz 25 LQFP-32(7x7) Microcontrollers RoHS | Exact Matches | https://www.lcsc.com/product-detail/C2054944.html
C481371 | MICROCHIP(美国微芯) | MIC39100-3.3WS-TR |  | SOT-223-4_L6.5-W3.5-P2.30-LS7.0-BR |  | U25 | 1 |  |  | MIC39100-3.3WS-TR | MICROCHIP | 1 | 1.1201 | 1.12 | C481371 | SOT-223 | 1 | 1 | 2500 | 2278 | In Stock |  | 3.3V Positive Fixed SOT-223 Voltage Regulators - Linear, Low Drop Out (LDO) Regulators RoHS | Exact Matches | https://www.lcsc.com/product-detail/C481371.html
C90770 | 杭州中科微 | ATGM336H-5N31 |  | GPSM-SMD_ATGM336H-TR |  | U27 | 1 |  |  | ATGM336H-5N31 | ZHONGKEWEI | 1 | 3.1611 | 3.16 | C90770 | SMD,10.1x9.7mm | 1 | 1 | 1000 | 4459 | In Stock |  | 2.5m -148dBm 2.7V~3.6V SMD,10.1x9.7mm RF Receivers RoHS | Exact Matches | https://www.lcsc.com/product-detail/C90770.html
C49446790 | YONGYUTAI(永裕泰) | XC6206-1.2V |  | SOT-23-3_L3.0-W1.6-P1.90-LS2.8-BR |  | U29 | 1 |  |  | XC6206-1.2V | YONGYUTAI | 10 | 0.0486 | 0.49 | C49446790 | SOT-23-3L | 10 | 10 | 3000 | 380 | In Stock |  | 1.2V Positive Fixed SOT-23-3L Voltage Regulators - Linear, Low Drop Out (LDO) Regulators RoHS | Exact Matches | https://www.lcsc.com/product-detail/C49446790.html
C2892669 | YONGYUTAI(永裕泰) | XC6206-2.8V |  | SOT-23-3_L2.9-W1.6-P1.90-LS2.8-BR |  | U30 | 1 |  |  | XC6206-2.8V | YONGYUTAI | 20 | 0.0428 | 0.86 | C2892669 | SOT-23-3L | 20 | 20 | 3000 | 5280 | In Stock |  | Linear Voltage Regulator IC Positive Fixed 1 Output 250mA SOT-23-3L | Exact Matches | https://www.lcsc.com/product-detail/C2892669.html
C1985532 | ABRACON | ABM11W-48.0000MHZ-7-B1U-T3 | 48MHz | CRYSTAL-SMD_4P-L2.0-W1.6-BL |  | U31 | 1 |  |  | ABM11W-48.0000MHZ-7-B1U-T3 | ABRACON | 1 | 0.5431 | 0.54 | C1985532 | SMD2016-4P | 1 | 1 | 3000 | 2358 | In Stock |  | Crystal 48MHz ±10ppm 7pF 40Ω SMD2016-4P | Exact Matches | https://www.lcsc.com/product-detail/C1985532.html
C2965508 | EBYTE(亿佰特) | E01C-ML01SP4 |  | COMM-SMD_E01C-ML01SP4 |  | U32 | 1 |  |  | E01C-ML01SP4 | EBYTE | 1 | 2.9004 | 2.90 | C2965508 | SMD,14.5x18mm | 1 | 1 | 1000 | 281 | In Stock |  | Transceiver 2.4GHz -96dBm 2km SPI SMD,14.5x18mm RF Transceiver Modules and Modems RoHS | Exact Matches | https://www.lcsc.com/product-detail/C2965508.html
C114409 | ST(意法半导体) | STM32H743VIT6 |  | LQFP-100_L14.0-W14.0-P0.50-LS16.0-BL |  | U33 | 1 |  |  | STM32H743VIT6 | ST | 1 | 8.9804 | 8.98 | C114409 | LQFP-100(14x14) | 1 | 1 | 90 | 3870 | In Stock |  | ARM Cortex-M7 32 Bit 480MHz 82 LQFP-100(14x14) Microcontrollers RoHS | Exact Matches | https://www.lcsc.com/product-detail/C114409.html
C7431054 | SHOU HAN(首韩) | SS12D10G5 |  | SW-TH_SHOU-HAN_SS12D10G4 |  | U34 | 1 |  |  | SS12D10G5 | SHOU HAN | 5 | 0.1759 | 0.88 | C7431054 | Through Hole,12.7x6.7mm | 5 | 5 | 500 | 42125 | In Stock |  | Slide Switch SPDT 2A @ 125V Through Hole 12.7mm | Exact Matches | https://www.lcsc.com/product-detail/C7431054.html
C19273151 | YONGYUTAI(永裕泰) | YLED0603G |  | LED0603-FD |  | U36 | 1 |  |  | YLED0603G | YONGYUTAI | 100 | 0.0061 | 0.61 | C19273151 | 0603 | 100 | 100 | 4000 | 120300 | In Stock |  | Emerald Green LED Indication - Discrete 2.7V~3.2V 0603 | Exact Matches | https://www.lcsc.com/product-detail/C19273151.html
C709357 | kinghelm(金航标) | KH-TYPE-C-16P |  | USB-C-SMD_KH-TYPE-C-16P |  | USB3 | 1 |  |  | KH-TYPE-C-16P | kinghelm | 5 | 0.0769 | 0.38 | C709357 | SMD | 5 | 5 | 1500 | 95380 | In Stock |  | USB-C (USB TYPE-C) Receptacle Connector 16 Position Surface Mount, Right Angle | Exact Matches | https://www.lcsc.com/product-detail/C709357.html

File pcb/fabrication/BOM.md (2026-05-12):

| No. | Quantity | Comment | Designator | Footprint | Value | Manufacturer Part | Manufacturer | Supplier Part | Supplier | LCSC Price | LCSC Stock | JLCPCB Price |
| --- | --- | --- | --- | --- | ----- | --- | --- | --- | --- | --- | --- | --- |
| 1 | 2 | 10uF | C1,C100 | C0603 | 10uF  | CL10A106KP8NNNC | SAMSUNG(三星) | [C19702](https://www.lcsc.com/product-detail/C19702.html) | LCSC | | | 0.0016 |
| 2 | 10 | 1uF | C2,C8,C9,C10,C51,C93,C107,C108,C109,C110 | C0402 | 1uF | CL05A105KO5NNNC | SAMSUNG(三星) | [C29266](https://www.lcsc.com/product-detail/C29266.html) | LCSC | | | 0.0005 |
| 3 | 43 | 100nF | C3,C7,C11,C12,C13,C14,C15,C16,C22,C24,C28,C29,C31,C32,C39,C40,C41,C43,C52,C53,C54,C60,C61,C62,C63,C66,C67,C69,C71,C75,C76,C77,C78,C79,C80,C81,C89,C92,C95,C105,C106,C114,C121 | C0402 | 100nF | CC0402X7R25V104KN | TORCH(火炬) | [C53084459](https://www.lcsc.com/product-detail/C53084459.html) | LCSC | | | 0.0004 |
| 4 | 12 | 22uF | C4,C5,C6,C36,C37,C38,C55,C57,C58,C59,C68,C70 | C0805 | 22uF  | CL21A226MAYNNNE | SAMSUNG(三星) | [C602037](https://www.lcsc.com/product-detail/C602037.html) | LCSC | | | 0.0064 |
| 5 | 3 | 2.2uF | C25,C115,C116 | C0603 | 2.2uF | CL10A225KO8NNNC | SAMSUNG(三星) | [C23630](https://www.lcsc.com/product-detail/C23630.html) | LCSC | | | 0.0011 |
| 6 | 1 | 10nF | C27 | C0603 | 10nF  | CC0603KRX7R9BB103 | YAGEO(国巨) | [C100042](https://www.lcsc.com/product-detail/C100042.html) | LCSC | | | 0.0004 |
| 7 | 1 | 4.7uF | C94 | C0603 | 4.7uF | CL10A475KO8NNNC | SAMSUNG(三星) | [C19666](https://www.lcsc.com/product-detail/C19666.html) | LCSC | | | 0.0017 |
| 8 | 1 | 10uF | C96 | C0805 | 10uF  | CL21B106KOQNNNE | SAMSUNG(三星) | [C95841](https://www.lcsc.com/product-detail/C95841.html) | LCSC | | | 0.0045 |
| 9 | 2 | 22uF | C97,C98 | C0603 | 22uF  | CL10A226MP8NUNE | SAMSUNG(三星) | [C86295](https://www.lcsc.com/product-detail/C86295.html) | LCSC | | | 0.0024 |
| 10  | 1 | 10uF | C99 | CAP-SMD_L3.2-W1.6-RD-C7171 | 10uF  | TAJA106K016RNJ | Kyocera AVX | [C7171](https://www.lcsc.com/product-detail/C7171.html) | LCSC | | | 0.0212 |
| 11  | 1 | 15pF | C103 | C0603 | 15pF  | CL10C150JB8NNNC | SAMSUNG(三星) | [C1644](https://www.lcsc.com/product-detail/C1644.html) | LCSC | | | 0.0009 |
| 12  | 2 | 10pF | C112,C113 | C0603 | 10pF  | CC0603JRNPO9BN100 | YAGEO(国巨) | [C106245](https://www.lcsc.com/product-detail/C106245.html) | LCSC | | | 0.0005 |
| 13  | 4 | 330uF | C117,C118,C119,C120 | CAP-SMD_BD6.3-L6.6-W6.6-LS7.2-FD_3 | 330uF | RVT16V330M6X8 | JIERR(捷而瑞) | [C47023104](https://www.lcsc.com/product-detail/C47023104.html) | LCSC | | | 0.0079 |
| 14  | 1 | XT60PW-M | CN1 | CONN-TH_XT60PW-M | | XT60PW-M | AMASS(艾迈斯) | [C98732](https://www.lcsc.com/product-detail/C98732.html) | LCSC | | | 0.0766 |
| 15  | 1 | FPC-05F-24PH20 | FPC1 | FPC-SMD_24P-P0.50_FPC-05F-24PH20 | | FPC-05F-24PH20 | XUNPU(讯普) | [C2856805](https://www.lcsc.com/product-detail/C2856805.html) | LCSC | | | 0.0148 |
| 16  | 5 | HX PH254-01-04-Z-L11.5 straight pin header | H1,H2,H3,H4,H5 | HDR-TH_4P-HX-PH254-01-04-Z-L11.5 | | HX PH254-01-04-Z-L11.5 straight pin header | hanxia(韩下) | [C52016392](https://www.lcsc.com/product-detail/C52016392.html) | LCSC | | | 0.0045 |
| 17  | 5 | BLM15PD121SN1D | L1,L2,L3,L4,L5 | L0402 | | BLM15PD121SN1D | muRata(村田) | [C76891](https://www.lcsc.com/product-detail/C76891.html) | LCSC | | | 0.0014 |
| 18  | 1 | 4.7uH | L6 | IND-SMD_L3.0-W3.0-1 | 4.7uH | ANR3015T4R7M | APV(爱普微) | [C7427089](https://www.lcsc.com/product-detail/C7427089.html) | LCSC | | | 0.0055 |
| 19  | 1 | 47nH | L7 | IND-SMD_L1.8-W1.0 | 47nH  | AHW1608C-47NJTF | APV(爱普微) | [C6807998](https://www.lcsc.com/product-detail/C6807998.html) | LCSC | | | 0.006 |
| 20  | 1 | BWGNSCNX18-18W4 | L8 | ANT-TH_L18.0-W18.0_C9900026472 | | BWGNSCNX18-18W4 | BAT WIRELESS(蝙蝠无线)  | [C784395](https://www.lcsc.com/product-detail/C784395.html) | LCSC | | | 0.1038 |
| 21  | 24 | IRLR7843TRPBF | Q1,Q2,Q3,Q4,Q5,Q6,Q7,Q8,Q9,Q10,Q11,Q12,Q13,Q14,Q15,Q16,Q17,Q18,Q19,Q20,Q21,Q22,Q23,Q24 | TO-252-3_L6.6-W6.1-P4.57-LS9.9-BR-CW | | IRLR7843TRPBF | TECH PUBLIC(台舟) | [C19268133](https://www.lcsc.com/product-detail/C19268133.html) | LCSC | | | |
| 22  | 24 | 10kΩ | R1,R2,R3,R4,R9,R10,R15,R21,R24,R30,R33,R34,R36,R41,R46,R47,R57,R58,R63,R64,R74,R75,R76,R85 | R0603 | 10kΩ  | RC0603FR-0710KL | YAGEO(国巨) | [C98220](https://www.lcsc.com/product-detail/C98220.html) | LCSC | | | 0.0003 |
| 23  | 25 | 33kΩ | R5,R6,R7,R8,R16,R17,R19,R20,R22,R23,R28,R29,R42,R43,R44,R45,R48,R49,R59,R60,R61,R62,R65,R66,R84 | R0603 | 33kΩ  | FRC0603F3302TS | FOJAN(富捷) | [C2907028](https://www.lcsc.com/product-detail/C2907028.html) | LCSC | | | 0.0002 |
| 24  | 4 | 2.2kΩ | R11,R12,R79,R80 | R0402 | 2.2kΩ | FRC0402J222 TS | FOJAN(富捷) | [C2906920](https://www.lcsc.com/product-detail/C2906920.html) | LCSC | | | 0.0001 |
| 25  | 18 | 270kΩ | R13,R14,R37,R38,R39,R40,R50,R51,R52,R53,R54,R55,R67,R68,R69,R70,R71,R72 | R0402 | 270kΩ | RC0402FR-07270KL | YAGEO(国巨) | [C163475](https://www.lcsc.com/product-detail/C163475.html) | LCSC | | | 0.0002 |
| 26  | 6 | 100kΩ | R18,R25,R26,R27,R31,R32 | R0402 | 100kΩ | RC0402FR-07100KL | YAGEO(国巨) | [C60491](https://www.lcsc.com/product-detail/C60491.html) | LCSC | | | 0.0002 |
| 27  | 1 | 1kΩ | R77 | R0402 | 1kΩ | RC0402FR-071KL | YAGEO(国巨) | [C106235](https://www.lcsc.com/product-detail/C106235.html) | LCSC | | | 0.0002 |
| 28  | 1 | 4.7kΩ | R78 | R0402 | 4.7kΩ | RC0402FR-074K7L | YAGEO(国巨) | [C105871](https://www.lcsc.com/product-detail/C105871.html) | LCSC | | | 0.0002 |
| 29  | 2 | 5.1kΩ | R81,R82 | R0603 | 5.1kΩ | FRC0603F5101TS | FOJAN(富捷) | [C2907044](https://www.lcsc.com/product-detail/C2907044.html) | LCSC | | | 0.0002 |
| 30  | 1 | 120Ω | R83 | R0402 | 120Ω  | FRC0402F1200TS | FOJAN(富捷) | [C2909315](https://www.lcsc.com/product-detail/C2909315.html) | LCSC | | | 0.0001 |
| 31  | 5 | LXW-4X3X2-SMD | SW1,SW2,SW3,SW4,SW5 | SW-SMD_L3.9-W3.0-LS5.0 | | LXW-4X3X2-SMD | LXWCONN(连兴旺电子) | [C53447012](https://www.lcsc.com/product-detail/C53447012.html) | LCSC | | | 0.0047 |
| 32  | 12 | MIC4605-1YM-TR | U1,U7,U10,U13,U14,U16,U17,U19,U20,U21,U22,U24 | SOIC-8_L4.9-W3.9-P1.27-LS6.0-BL | | MIC4605-1YM-TR | MICROCHIP(美国微芯) | [C628051](https://www.lcsc.com/product-detail/C628051.html) | LCSC | | | 0.2001 |
| 33  | 1 | ICM-42688-P | U2 | LGA-14_L3.0-W2.5-P0.50-TL | | ICM-42688-P | TDK InvenSense(应美盛) | [C1850418](https://www.lcsc.com/product-detail/C1850418.html) | LCSC | | | 1.8903 |
| 34  | 1 | BMP280 | U3 | LGA-8_L2.5-W2.0-P0.65_AMP6127 | | BMP280 | Bosch(博世) | [C83291](https://www.lcsc.com/product-detail/C83291.html) | LCSC | | | 0.9282 |
| 35  | 1 | LIS3MDLTR | U4 | LGA-12_L2.0-W2.0-P0.50-BL | | LIS3MDLTR | ST(意法半导体) | [C478483](https://www.lcsc.com/product-detail/C478483.html) | LCSC | | | 0.7407 |
| 36  | 5 | 2.54-1P TPGT | U5,U6,U8,U12,U35 | SW-SMD_2P-L6.2-W2.5-LS9.4 | | 2.54-1P TPGT | SHOU HAN(首韩) | [C7421519](https://www.lcsc.com/product-detail/C7421519.html) | LCSC | | | 0.0681 |
| 37  | 3 | STM32F303K8T6 | U9,U15,U18 | LQFP-32_L7.0-W7.0-P0.80-LS9.0-BL | | STM32F303K8T6 | ST(意法半导体) | [C118318](https://www.lcsc.com/product-detail/C118318.html) | LCSC | | | 1.0937 |
| 38  | 1 | AP63205WU-7 | U11 | TSOT-23-6_L2.9-W1.6-P0.95-LS2.8-BL | | AP63205WU-7 | DIODES(美台) | [C2071056](https://www.lcsc.com/product-detail/C2071056.html) | LCSC | | | 0.0702 |
| 39  | 1 | STM32F051K8T6TR | U23 | LQFP-32_L7.0-W7.0-P0.80-LS9.0-BL | | STM32F051K8T6TR | ST(意法半导体) | [C2054944](https://www.lcsc.com/product-detail/C2054944.html) | LCSC | | | 0.2346 |
| 40  | 1 | MIC39100-3.3WS-TR | U25 | SOT-223-4_L6.5-W3.5-P2.30-LS7.0-BR | | MIC39100-3.3WS-TR | MICROCHIP(美国微芯) | [C481371](https://www.lcsc.com/product-detail/C481371.html) | LCSC | | | 0.1644 |
| 41  | 1 | ATGM336H-5N31 | U27 | GPSM-SMD_ATGM336H-TR | | ATGM336H-5N31 | 杭州中科微 | [C90770](https://www.lcsc.com/product-detail/C90770.html) | LCSC | | | 0.4641 |
| 42  | 1 | XC6206-1.2V | U29 | SOT-23-3_L3.0-W1.6-P1.90-LS2.8-BR | | XC6206-1.2V | YONGYUTAI(永裕泰) | [C49446790](https://www.lcsc.com/product-detail/C49446790.html) | LCSC | | | 0.0073 |
| 43  | 1 | XC6206-2.8V | U30 | SOT-23-3_L2.9-W1.6-P1.90-LS2.8-BR | | XC6206-2.8V | YONGYUTAI(永裕泰) | [C2892669](https://www.lcsc.com/product-detail/C2892669.html) | LCSC | | | 0.0064 |
| 44  | 1 | 48MHz | U31 | CRYSTAL-SMD_4P-L2.0-W1.6-BL | 48MHz | ABM11W-48.0000MHZ-7-B1U-T3 | ABRACON | [C1985532](https://www.lcsc.com/product-detail/C1985532.html) | LCSC | | | 0.0797 |
| 45  | 1 | E01C-ML01SP4 | U32 | COMM-SMD_E01C-ML01SP4 | | E01C-ML01SP4 | EBYTE(亿佰特) | [C2965508](https://www.lcsc.com/product-detail/C2965508.html) | LCSC | | | 0.4287 |
| 46  | 1 | STM32H743VIT6 | U33 | LQFP-100_L14.0-W14.0-P0.50-LS16.0-BL | | STM32H743VIT6 | ST(意法半导体) | [C114409](https://www.lcsc.com/product-detail/C114409.html) | LCSC | | | 1.323 |
| 47  | 1 | SS12D10G5 | U34 | SW-TH_SHOU-HAN_SS12D10G4 | | SS12D10G5 | SHOU HAN(首韩) | [C7431054](https://www.lcsc.com/product-detail/C7431054.html) | LCSC | | | 0.0259 |
| 48  | 1 | YLED0603G | U36 | LED0603-FD | | YLED0603G | YONGYUTAI(永裕泰) | [C19273151](https://www.lcsc.com/product-detail/C19273151.html) | LCSC | | | 0.001 |
| 49  | 1 | KH-TYPE-C-16P | USB3 | USB-C-SMD_KH-TYPE-C-16P | | KH-TYPE-C-16P | kinghelm(金航标) | [C709357](https://www.lcsc.com/product-detail/C709357.html) | LCSC | | | 0.0114 |

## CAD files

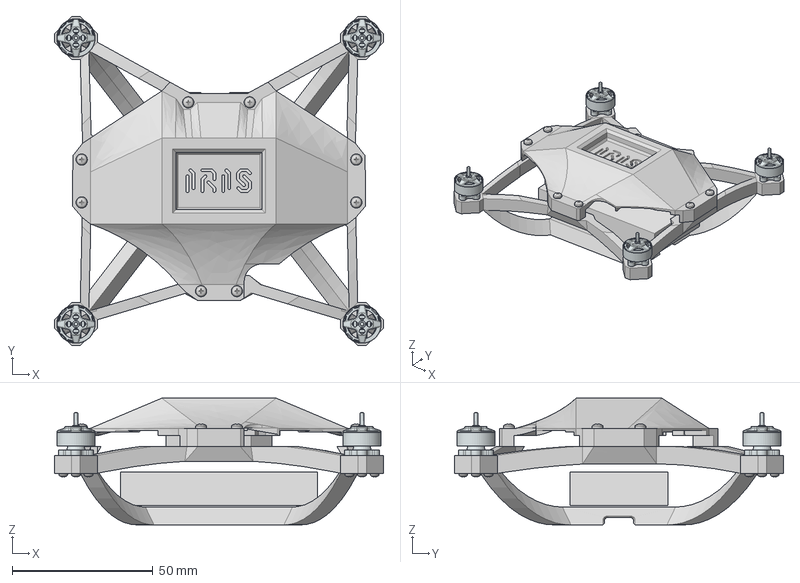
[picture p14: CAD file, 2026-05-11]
frame/IRIS_Assembly.step
116.8 x 116.8 x 45.0 mm
ISO 7045 - M1.6 x 8 - H Steel 4.6 Plain x 16
ISO 7045 - M2 x 10 - H Steel 4.6 Plain x 8

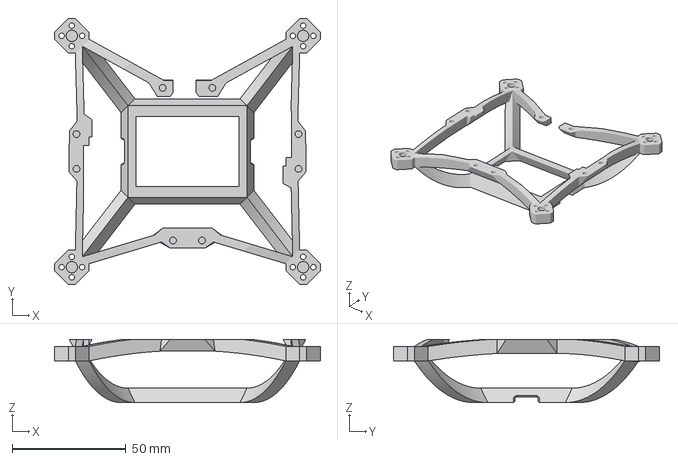
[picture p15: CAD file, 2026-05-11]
frame/3mf/frame_base.3mf
116.8 x 116.8 x 27.7 mm

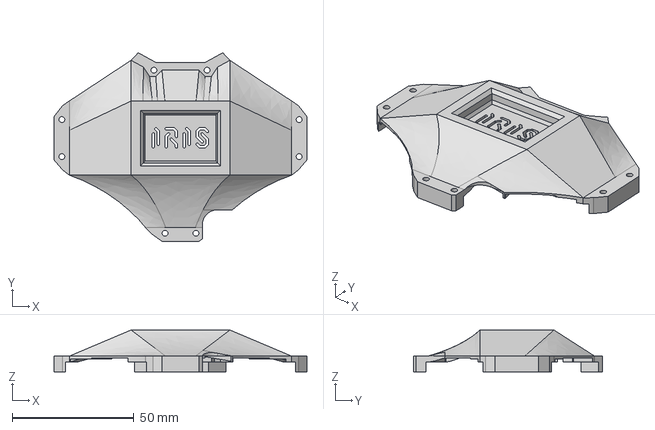
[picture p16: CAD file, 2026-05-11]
frame/pcb_cover.step
104.0 x 77.5 x 17.2 mm

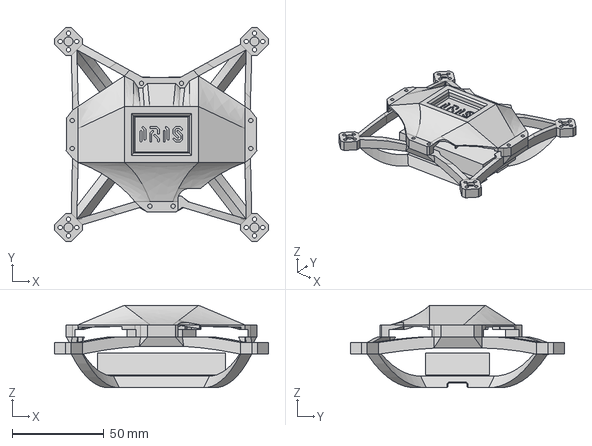
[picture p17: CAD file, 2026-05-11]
frame/frame_bottom.step
116.8 x 116.8 x 45.0 mm

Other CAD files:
frame/3mf/frame_pcb_cover.3mf
docs/render/IRIS.blend
docs/render/Skittle.blend
docs/render/frame_sliced.blend
docs/render/zine_background.blend
frame/stl/frame_base.stl
frame/stl/frame_pcb_cover.stl

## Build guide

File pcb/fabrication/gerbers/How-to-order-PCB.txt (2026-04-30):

How to Order PCB

Please refer to:
https://prodocs.easyeda.com/en/pcb/order-order-pcb/index.html

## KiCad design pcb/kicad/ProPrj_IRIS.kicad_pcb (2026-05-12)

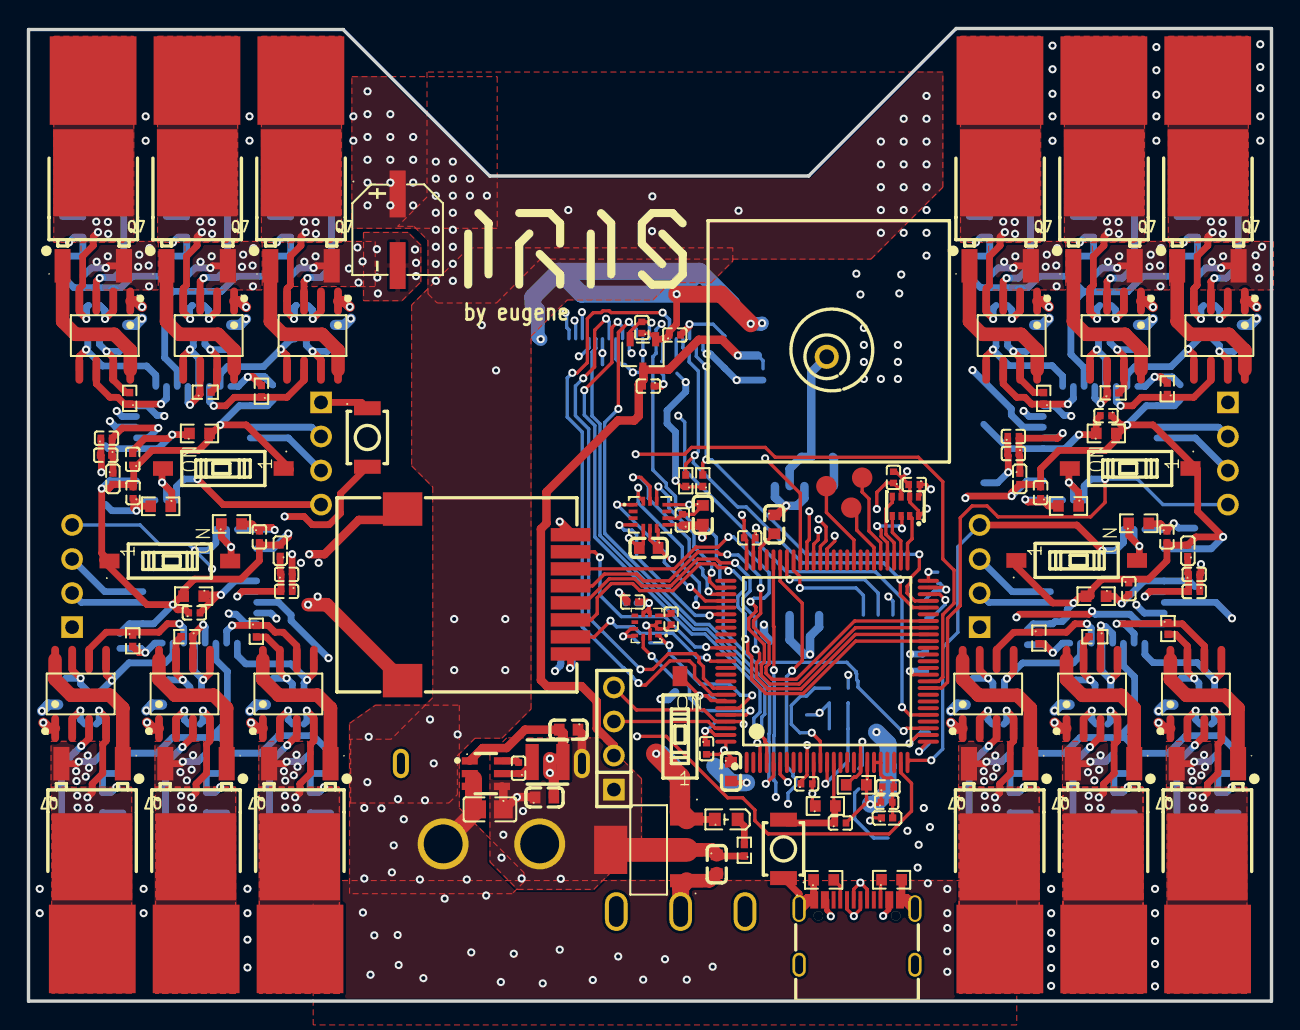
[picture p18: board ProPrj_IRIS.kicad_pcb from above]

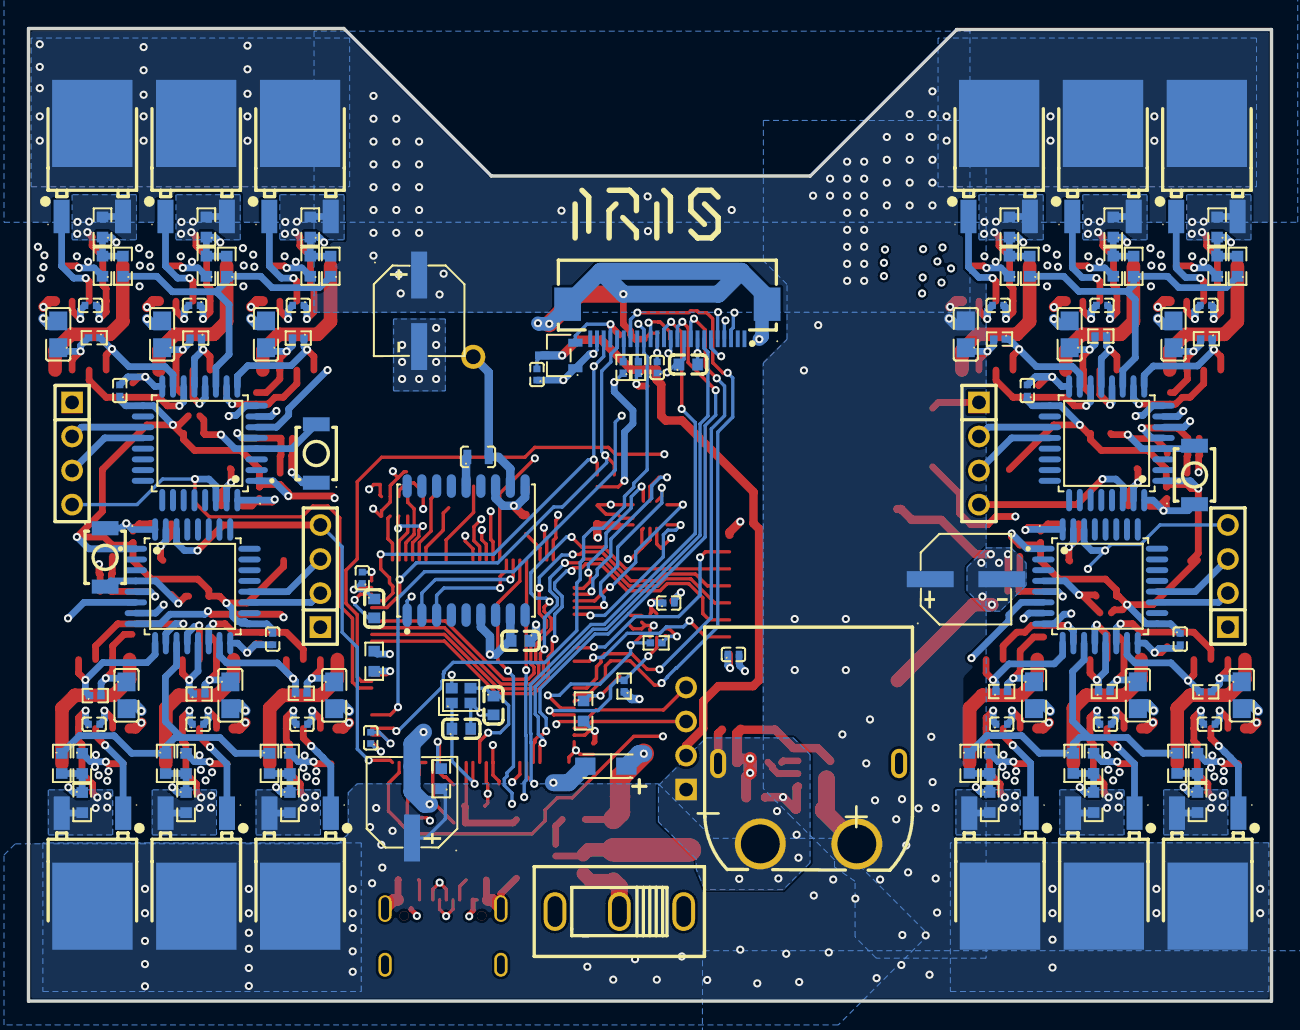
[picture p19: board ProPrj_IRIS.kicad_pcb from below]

Board: 4 copper layers, 92.7 x 72.5 mm, 244 parts (128 on the bottom side), 176 nets.

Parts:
C1, C25, C27, C94, C97, C98, C100, C103, C112, C113, C115, C116: C0603
C2, C3, C7, C8, C9, C10, C11, C12, C13, C14, C15, C16, C22, C24, C28, C29, C31, C32, C39, C40, C41, C43, C51, C52, C53, C54, C60, C61, C62, C63, C66, C67, C69, C71, C75, C76, C77, C78, C79, C80, C81, C89, C92, C93, C95, C105, C106, C107, C108, C109, C110, C114, C121: C0402
C4, C5, C6, C36, C37, C38, C55, C57, C58, C59, C68, C70, C96: C0805
C99: CAP-SMD_L3.2-W1.6-RD-C7171
C117, C118, C119, C120: CAP-SMD_BD6.3-L6.6-W6.6-LS7.2-FD_3
CN1: CONN-TH_XT60PW-M
FPC1: FPC-SMD_24P-P0.50_FPC-05F-24PH20
H1, H2, H3, H4, H5: HDR-TH_4P-HX-PH254-01-04-Z-L11.5
L1, L2, L3, L4, L5: L0402
L6: IND-SMD_L3.0-W3.0-1
L7: IND-SMD_L1.8-W1.0
L8: ANT-TH_L18.0-W18.0_C9900026472
Q1, Q2, Q3, Q4, Q5, Q6, Q7, Q8, Q9, Q10, Q11, Q12, Q13, Q14, Q15, Q16, Q17, Q18, Q19, Q20, Q21, Q22, Q23, Q24: TO-252-3_L6.6-W6.1-P4.57-LS9.9-BR-CW
R1, R2, R3, R4, R5, R6, R7, R8, R9, R10, R15, R16, R17, R19, R20, R21, R22, R23, R24, R28, R29, R30, R33, R34, R36, R41, R42, R43, R44, R45, R46, R47, R48, R49, R57, R58, R59, R60, R61, R62, R63, R64, R65, R66, R74, R75, R76, R81, R82, R84, R85: R0603
R11, R12, R13, R14, R18, R25, R26, R27, R31, R32, R37, R38, R39, R40, R50, R51, R52, R53, R54, R55, R67, R68, R69, R70, R71, R72, R77, R78, R79, R80, R83: R0402
SW1, SW2, SW3, SW4, SW5: SW-SMD_L3.9-W3.0-LS5.0
U1, U7, U10, U13, U14, U16, U17, U19, U20, U21, U22, U24: SOIC-8_L4.9-W3.9-P1.27-LS6.0-BL
U2: LGA-14_L3.0-W2.5-P0.50-TL
U3: LGA-8_L2.5-W2.0-P0.65_AMP6127
U4: LGA-12_L2.0-W2.0-P0.50-BL
U5, U6, U8, U12, U35: SW-SMD_2P-L6.2-W2.5-LS9.4
U9, U15, U18, U23: LQFP-32_L7.0-W7.0-P0.80-LS9.0-BL
U11: TSOT-23-6_L2.9-W1.6-P0.95-LS2.8-BL
U25: SOT-223-4_L6.5-W3.5-P2.30-LS7.0-BR
U27: GPSM-SMD_ATGM336H-TR
U29: SOT-23-3_L3.0-W1.6-P1.90-LS2.8-BR
U30: SOT-23-3_L2.9-W1.6-P1.90-LS2.8-BR
U31: CRYSTAL-SMD_4P-L2.0-W1.6-BL
U32: COMM-SMD_E01C-ML01SP4
U33: LQFP-100_L14.0-W14.0-P0.50-LS16.0-BL
U34: SW-TH_SHOU-HAN_SS12D10G4
U36: LED0603-FD
USB3: USB-C-SMD_KH-TYPE-C-16P

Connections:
1.2V: C108.2, FPC1.15, U29.2
2.8V: C109.2, FPC1.21, U30.2
3V3: C13.1, C14.1, C15.1, C16.1, C22.2, C25.2, C27.2, C28.1, C29.1, C31.1, C40.2, C43.1, C51.1, C52.1, C61.2, C63.1, C66.2, C75.1, C77.2, C78.2, C79.2, C80.2, C81.2, C94.1, C99.1, C100.2, C105.2, C106.1, C114.1, FPC1.14, L1.2, L2.2, L3.2, L4.1, L5.2, R2.2, R11.1, R12.1, R34.2, R36.2, R57.2, R76.1, R78.1, R79.1, R80.1, U2.5, U2.8, U3.6, U3.8, U4.5, U4.6, U4.9, U4.10, U5.1, U6.1, U8.1, U9.1, U9.17, U12.1, U15.1, U15.17, U18.1, U18.17, U23.1, U23.17, U25.3, U27.6, U27.8, U32.1, U33.6, U33.11, U33.27, U33.50, U33.75, U33.100, U35.1, U36.1
5V_USB: U34.3, USB3.A4, USB3.A9, USB3.B4, USB3.B9
7.4V_BATTERY: C4.2, C5.2, C6.2, C36.2, C37.2, C38.2, C55.2, C57.2, C58.2, C59.2, C68.2, C70.2, C96.2, C117.1, C118.1, C119.1, C120.1, CN1.2, Q1.2, Q3.2, Q5.2, Q8.2, Q9.2, Q11.2, Q14.2, Q15.2, Q17.2, Q20.2, Q21.2, Q23.2, R84.1, U1.1, U7.1, U10.1, U11.2, U11.3, U13.1, U14.1, U16.1, U17.1, U19.1, U20.1, U21.1, U22.1, U24.1
$1I45090\$1N2345: Q5.1, U22.3
$1I45090\$1N2351: Q4.1, U21.8
$1I45090\$1N2355: C69.2, U21.2
$1I45090\$1N2357: Q3.1, U21.3
$1I45090\$1N2360: Q2.1, U20.8
$1I45090\$1N2369: C67.2, U20.2
$1I45090\$1N2370: Q1.1, U20.3
$1I45090\$1N2393: C71.2, U22.2
$1I45090\$1N2396: Q6.1, U22.8
$1I45090\$1N2406: C2.2, C89.1, L3.1, U18.5
$1I45090\$1N39368: C13.2, R36.1, SW1.2, U18.4
$1I45090\AU: R19.1, R20.2, R21.2, U18.6
$1I45090\AV: R22.1, R23.2, R24.2, U18.7
$1I45090\AW: R28.1, R29.2, R30.2, U18.8
$1I45090\A_REF: R20.1, R23.1, R29.1, U18.11
$1I45090\BOOT0_ESC: R75.1, U18.31, U35.2
$1I45090\PHASE_U: C67.1, Q1.3, Q2.2, R19.2, U20.4
$1I45090\PHASE_V: C69.1, Q3.3, Q4.2, R22.2, U21.4
$1I45090\PHASE_W: C71.1, Q5.3, Q6.2, R28.2, U22.4
$1I45090\UH: R14.1, U18.9, U20.5
$1I45090\UL: R13.1, U18.10, U20.6
$1I45090\USART1_RX: H1.3, U18.20
$1I45090\USART1_TX: H1.2, U18.19
$1I45090\VH: R38.1, U18.13, U21.5
$1I45090\VL: R37.1, U18.12, U21.6
$1I45090\WH: R40.1, U18.15, U22.5
$1I45090\WL: R39.1, U18.14, U22.6
$1I45112\$1N2345: Q8.1, U1.3
$1I45112\$1N2351: Q7.1, U10.8
$1I45112\$1N2355: C24.2, U10.2
$1I45112\$1N2357: Q9.1, U10.3
$1I45112\$1N2360: Q10.1, U7.8
$1I45112\$1N2369: C7.2, U7.2
$1I45112\$1N2370: Q11.1, U7.3
$1I45112\$1N2393: C32.2, U1.2
$1I45112\$1N2396: Q12.1, U1.8
$1I45112\$1N2406: C3.1, C8.2, L1.1, U9.5
$1I45112\$1N39368: C14.2, R2.1, SW2.2, U9.4
$1I45112\AU: R8.1, R15.2, R17.2, U9.6
$1I45112\AV: R7.1, R9.2, R16.2, U9.7
$1I45112\AW: R4.2, R5.2, R6.1, U9.8
$1I45112\A_REF: R5.1, R16.1, R17.1, U9.11
$1I45112\BOOT0_ESC: R1.1, U5.2, U9.31
$1I45112\PHASE_U: C7.1, Q10.2, Q11.3, R8.2, U7.4
$1I45112\PHASE_V: C24.1, Q7.2, Q9.3, R7.2, U10.4
$1I45112\PHASE_W: C32.1, Q8.3, Q12.2, R6.2, U1.4
$1I45112\UH: R32.1, U7.5, U9.9
$1I45112\UL: R27.1, U7.6, U9.10
$1I45112\USART1_RX: H3.3, U9.20
$1I45112\USART1_TX: H3.2, U9.19
$1I45112\VH: R31.1, U9.13, U10.5
$1I45112\VL: R25.1, U9.12, U10.6
$1I45112\WH: R18.1, U1.5, U9.15
$1I45112\WL: R26.1, U1.6, U9.14
$1I45134\$1N2345: Q14.1, U13.3
$1I45134\$1N2351: Q13.1, U16.8
$1I45134\$1N2355: C41.2, U16.2
$1I45134\$1N2357: Q15.1, U16.3
$1I45134\$1N2360: Q16.1, U14.8
$1I45134\$1N2369: C39.2, U14.2
$1I45134\$1N2370: Q17.1, U14.3
$1I45134\$1N2393: C54.2, U13.2
$1I45134\$1N2396: Q18.1, U13.8
$1I45134\$1N2406: C9.2, C11.1, L2.1, U15.5
$1I45134\$1N39368: C15.2, R34.1, SW3.2, U15.4
$1I45134\AU: R45.1, R47.2, R49.2, U15.6
$1I45134\AV: R44.1, R46.2, R48.2, U15.7
$1I45134\AW: R41.2, R42.2, R43.1, U15.8
$1I45134\A_REF: R42.1, R48.1, R49.1, U15.11
$1I45134\BOOT0_ESC: R3.1, U6.2, U15.31
$1I45134\PHASE_U: C39.1, Q16.2, Q17.3, R45.2, U14.4
$1I45134\PHASE_V: C41.1, Q13.2, Q15.3, R44.2, U16.4
$1I45134\PHASE_W: C54.1, Q14.3, Q18.2, R43.2, U13.4
$1I45134\UH: R55.1, U14.5, U15.9
$1I45134\UL: R53.1, U14.6, U15.10
$1I45134\USART1_RX: H4.3, U15.20
$1I45134\USART1_TX: H4.2, U15.19
$1I45134\VH: R54.1, U15.13, U16.5
$1I45134\VL: R51.1, U15.12, U16.6
$1I45134\WH: R50.1, U13.5, U15.15
$1I45134\WL: R52.1, U13.6, U15.14
$1I45156\$1N2345: Q20.1, U17.3
$1I45156\$1N2351: Q19.1, U24.8
$1I45156\$1N2355: C62.2, U24.2
$1I45156\$1N2357: Q21.1, U24.3
$1I45156\$1N2360: Q22.1, U19.8
$1I45156\$1N2369: C60.2, U19.2
$1I45156\$1N2370: Q23.1, U19.3
$1I45156\$1N2393: C76.2, U17.2
$1I45156\$1N2396: Q24.1, U17.8
$1I45156\$1N2406: C10.2, C12.1, L5.1, U23.5
$1I45156\$1N39368: C16.2, R57.1, SW4.2, U23.4
$1I45156\AU: R62.1, R64.2, R66.2, U23.6
$1I45156\AV: R61.1, R63.2, R65.2, U23.7
$1I45156\AW: R58.2, R59.2, R60.1, U23.8
$1I45156\A_REF: R59.1, R65.1, R66.1, U23.11
$1I45156\BOOT0_ESC: R10.1, U8.2, U23.31
$1I45156\PHASE_U: C60.1, Q22.2, Q23.3, R62.2, U19.4
$1I45156\PHASE_V: C62.1, Q19.2, Q21.3, R61.2, U24.4
$1I45156\PHASE_W: C76.1, Q20.3, Q24.2, R60.2, U17.4
$1I45156\UH: R72.1, U19.5, U23.9
$1I45156\UL: R70.1, U19.6, U23.10
$1I45156\USART1_RX: H5.3, U23.20
$1I45156\USART1_TX: H5.2, U23.19
$1I45156\VH: R71.1, U23.13, U24.5
$1I45156\VL: R68.1, U23.12, U24.6
$1I45156\WH: R67.1, U17.5, U23.15
$1I45156\WL: R69.1, U17.6, U23.14
$1N17368: C97.2, C98.2, L6.2, U11.1, U34.1
$1N17546: C95.1, L6.1, U11.5
$1N56559: C95.2, U11.6
$1N79325: L7.2, L8.1, U27.11
$1N79329: L7.1, U27.14
$1N81168: FPC1.17, R77.2
$1N85586: R81.1, USB3.B5
$1N85625: R82.2, USB3.A5
$1N96765: C121.1, R76.2, SW5.2, U33.14
$1N102666: C115.2, U33.73
$1N105569: C116.2, U33.48
$1N119973: C53.2, U4.4
$1N130959: R83.2, U36.2
$1N133579: R84.2, R85.2, U33.18
+5V: C1.2, C107.2, C110.2, H2.2, U25.1, U29.3, U30.3, U34.2
BOOT0: R33.1, U12.2, U33.94
BOOT1: R74.1, U33.36
CAM_RST: FPC1.19, R78.2
CAM_XCLK: FPC1.12, U33.67
DCMI_0: FPC1.6, U33.63
DCMI_1: FPC1.4, U33.64
DCMI_2: FPC1.3, U33.65
DCMI_3: FPC1.5, U33.66
DCMI_4: FPC1.7, U33.3
DCMI_5: FPC1.9, U33.92
DCMI_6: FPC1.11, U33.4
DCMI_7: FPC1.13, U33.5
DCMI_HSYNC: FPC1.16, U33.28
DCMI_PXLCLK: C103.2, FPC1.8, U33.30
DCMI_VSYNC: FPC1.18, U33.93
DM: U33.70, USB3.A7, USB3.B7
DP: U33.71, USB3.A6, USB3.B6
E01_CE: U32.2, U33.88
E01_IRQ: U32.7, U33.86
GND: C1.1, C2.1, C3.2, C4.1, C5.1, C6.1, C8.1, C9.1, C10.1, C11.2, C12.2, C22.1, C25.1, C27.1, C28.2, C29.2, C31.2, C36.1, C37.1, C38.1, C40.1, C43.2, C51.2, C52.2, C53.1, C55.1, C57.1, C58.1, C59.1, C61.1, C63.2, C66.1, C68.1, C70.1, C75.2, C77.1, C78.1, C79.1, C80.1, C81.1, C89.2, C92.1, C93.1, C94.2, C96.1, C97.1, C98.1, C99.2, C100.1, C103.1, C105.1, C106.2, C107.1, C108.1, C109.1, C110.1, C112.2, C113.2, C114.2, C115.1, C116.1, C117.2, C118.2, C119.2, C120.2, C121.2, CN1.1, CN1.3, CN1.4, FPC1.10, FPC1.23, FPC1.25, FPC1.26, H1.1, H2.1, H3.1, H4.1, H5.1, Q2.3, Q4.3, Q6.3, Q7.3, Q10.3, Q12.3, Q13.3, Q16.3, Q18.3, Q19.3, Q22.3, Q24.3, R1.2, R3.2, R4.1, R9.1, R10.2, R13.2, R14.2, R15.1, R18.2, R21.1, R24.1, R25.2, R26.2, R27.2, R30.1, R31.2, R32.2, R33.2, R37.2, R38.2, R39.2, R40.2, R41.1, R46.1, R47.1, R50.2, R51.2, R52.2, R53.2, R54.2, R55.2, R58.1, R63.1, R64.1, R67.2, R68.2, R69.2, R70.2, R71.2, R72.2, R74.2, R75.2, R77.1, R81.2, R82.1, R83.1, R85.1, SW1.1, SW2.1, SW3.1, SW4.1, SW5.1, U1.7, U2.6, U2.7, U2.9, U2.11, U3.1, U3.7, U4.2, U4.3, U4.12, U7.7, U9.16, U9.32, U10.7, U11.4, U13.7, U14.7, U15.16, U15.32, U16.7, U17.7, U18.16, U18.32, U19.7, U20.7, U21.7, U22.7, U23.16, U23.32, U24.7, U25.2, U25.4, U27.1, U27.10, U27.12, U29.1, U30.1, U31.2, U31.4, U32.8, U32.9, U32.10, U33.10, U33.19, U33.26, U33.49, U33.74, U33.99, USB3.1, USB3.2, USB3.3, USB3.4, USB3.A1, USB3.A12, USB3.B1, USB3.B12
GPS_RX_MCU_TX: U27.3, U33.68
GPS_TX_MCU_RX: U27.2, U33.69
I2C1_SCLK: R12.2, U4.1, U33.95
I2C1_SDA: R11.2, U4.11, U33.96
I2C2_SCLK: FPC1.20, R80.2, U33.46
I2C2_SDA: FPC1.22, R79.2, U33.47
IMU_INT: U2.4, U33.81
MOTOR1: H1.4, U18.30, U33.34
MOTOR2: H3.4, U9.30, U33.35
MOTOR3: H5.4, U23.30, U33.24
MOTOR4: H4.4, U15.30, U33.25
RADIO_RX: H2.4, U33.97
RADIO_TX: H2.3, U33.98
SPI2_CS: U3.2, U33.51
SPI2_MISO: U3.5, U33.53
SPI2_MOSI: U3.3, U33.54
SPI2_SCLK: U3.4, U33.52
SPI3_CS: U2.12, U33.77
SPI3_MISO: U2.1, U33.79
SPI3_MOSI: U2.14, U33.80
SPI3_SCLK: U2.13, U33.78
SPI4_CS: U32.3, U33.41
SPI4_MISO: U32.6, U33.43
SPI4_MOSI: U32.5, U33.44
SPI4_SCLK: U32.4, U33.42
VDDA: C92.2, C93.2, L4.2, U33.20, U33.21
XI_HS: C113.1, U31.3, U33.12
XO_HS: C112.1, U31.1, U33.13

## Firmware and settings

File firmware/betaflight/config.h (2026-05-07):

/*
 * This file is part of Betaflight.
 *
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
 * See the GNU General Public License for more details.
 *
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
 * If not, see <http://www.gnu.org/licenses/>.
 */

#pragma once

#define FC_TARGET_MCU     STM32H743
#define BOARD_NAME IRIS
#define MANUFACTURER_ID EUGENE_IS_AWESOME

#define USE_ACC
#define USE_ACC_SPI_ICM42688P
#define USE_GYRO
#define USE_GYRO_SPI_ICM42688P
#define USE_BARO
#define USE_BARO_SPI_BMP280
#define USE_MAG
#define USE_MAG_LIS3MDL
// #define USE_FLASH
// #define USE_FLASH_M25P16
// #define USE_MAX7456

// #define BEEPER_PIN PD15
#define MOTOR1_PIN PB0
#define MOTOR2_PIN PB1
#define MOTOR3_PIN PA2
#define MOTOR4_PIN PA3
// #define RX_PPM_PIN PA3
// #define LED_STRIP_PIN PD12
#define UART1_TX_PIN PA9  // GPS
#define UART2_TX_PIN PA2
#define UART3_TX_PIN PB10
#define UART4_TX_PIN PA0
#define UART6_TX_PIN PC6
#define UART7_TX_PIN PE8
#define UART8_TX_PIN PE1  // nanoELRS
#define UART1_RX_PIN PA10 // GPS 
#define UART2_RX_PIN PA3
#define UART3_RX_PIN PB11
#define UART4_RX_PIN PA1
#define UART6_RX_PIN PC7
#define UART7_RX_PIN PE7
#define UART8_RX_PIN PE0  // nanoELRS
#define I2C1_SCL_PIN PB8
#define I2C1_SDA_PIN PB9
// #define I2C2_SCL_PIN PB10 // OV2640 camera
// #define I2C2_SDA_PIN PB11 // OV2640 camera
#define LEPD_PIN PC13

#define SPI1_SCK_PIN PA5
#define SPI1_SDI_PIN PA6
#define SPI1_SDO_PIN PA7

#define SPI2_SCK_PIN PB13
#define SPI2_SDI_PIN PB14
#define SPI2_SDO_PIN PB15

#define SPI3_SCK_PIN PC10
#define SPI3_SDI_PIN PC11
#define SPI3_SDO_PIN PC12

#define SPI4_SCK_PIN PE12
#define SPI4_SDI_PIN PE13
#define SPI4_SDO_PIN PE14
// #define CAMERA_CONTROL_PIN PC8
#define ADC_VBAT_PIN PC3
#define ADC_RSSI_PIN PC5
#define ADC_CURR_PIN PC2
// #define FLASH_CS_PIN PA15
// #define MAX7456_SPI_CS_PIN PE4
#define GYRO_1_EXTI_PIN PD0
#define GYRO_1_CS_PIN PA15
#define BARO_CS_PIN PB12

#define TIMER_PIN_MAPPING \
    TIMER_PIN_MAP( 3, PB0,  2,  0 ) \
    TIMER_PIN_MAP( 4, PB1,  2,  1 ) \
    TIMER_PIN_MAP( 5, PA2,  1,  2 ) \
    TIMER_PIN_MAP( 6, PA3,  1,  3 ) \

// TIMER_PIN_MAP( 0, PD12, 1, 10 )
// TIMER_PIN_MAP( 1, PA3,  1,  0 )
// TIMER_PIN_MAP( 2, PC8,  2,  0 ) 

#define ADC1_DMA_OPT 8
#define ADC3_DMA_OPT 9
#define TIMUP1_DMA_OPT 0
#define TIMUP2_DMA_OPT 0
#define TIMUP3_DMA_OPT 0
#define TIMUP4_DMA_OPT 0
#define TIMUP8_DMA_OPT 0

#define BARO_SPI_INSTANCE SPI2
#define MAG_I2C_INSTANCE I2CDEV_1
#define ADC_INSTANCE ADC1
// #define DEFAULT_BLACKBOX_DEVICE BLACKBOX_DEVICE_FLASH
#define DEFAULT_CURRENT_METER_SOURCE CURRENT_METER_ADC
#define DEFAULT_VOLTAGE_METER_SOURCE VOLTAGE_METER_ADC
#define DEFAULT_VOLTAGE_METER_SCALE 110
#define DEFAULT_CURRENT_METER_SCALE 200
// #define BEEPER_INVERTED
// #define MAX7456_SPI_INSTANCE SPI4
// #define FLASH_SPI_INSTANCE SPI3
#define GYRO_1_SPI_INSTANCE SPI3

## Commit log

2026-04-15 STM32F407 design backup
2026-04-20 finished PCB, slightly oversized
2026-04-30 PCB Version 2, 50% size reduction + finished gerbers
    [Drill_NPTH_Through.DRL, Drill_PTH_Through.DRL, Drill_PTH_Through_Via.DRL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]
2026-05-01 (minor fix for PCB V2) CAM_XCLK connected
    [Drill_NPTH_Through.DRL, Drill_PTH_Through.DRL, Drill_PTH_Through_Via.DRL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]
2026-05-03 Moved the 5V power switch for the frame mount
2026-05-04 Fixed camera placement and finalized PCB component BOM
    [BOM_Board1_PCB1_2026-05-03.csv, BOM_Board1_PCB1_2026-05-03.xlsx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]
2026-05-04 Moved boot selector switches for easier soldering
    [Drill_NPTH_Through.DRL, Drill_PTH_Through.DRL, Drill_PTH_Through_Via.DRL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]
2026-05-04 converted PCB design to KiCAD + blender 3D model for renders
    [IRIS_KiCAD.kicad_pcb, IRIS_KiCAD.kicad_sch]
2026-05-05 flipped XT60 connector to bottom + photorealistic renders
    [IRIS_KiCAD.kicad_pcb, IRIS_KiCAD.kicad_sch]
2026-05-06 3D printable drone frame
    [frame_base.3mf, frame_base.stl, frame_pcb_cover.3mf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]
2026-05-06 reorganized repository
    [BOM_Board1_PCB1_2026-05-03.csv, BOM_Board1_PCB1_2026-05-03.xlsx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]
2026-05-06 drone frame assembly, components, design
2026-05-07 firmware for flight controller
    [frame_sliced.blend]
2026-05-08 Cool logo design
    [frame_sliced.blend, logo.kicad_pcb, logo.kicad_sch]
2026-05-10 updates to ESC, quality-of-life improvements to the PCB, redesigned frame top, more photorealistic renders
    [BOM_Board1_PCB1.csv, BOM_Board1_PCB1.xlsx, BOM_Board1_PCB1_2026-05-03.csv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]
2026-05-10 completed drone assembly
    [IRIS_Assembly.step, LCSC_BOM_export.xls, frame_bottom.step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]
2026-05-10 improved bill of materials
    [BOM.csv]
2026-05-11 'hero shot' render + orthogonal renders + updated README
    [IRIS.blend]
2026-05-11 camera attachment point + zip tie grooves
    [IRIS_Assembly.step, frame_base.3mf, frame_base.stl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]
2026-05-12 magazine page
    [IRIS.blend, Skittle.blend, frame_sliced.blend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]
2026-05-12 cleaned up README
    [IRIS.blend, zine_background.blend]
2026-05-12 corrected nrst decoupling capacitor - thanks to @kaipereira for the tip
    [Drill_NPTH_Through.DRL, Drill_PTH_Through.DRL, Drill_PTH_Through_Via.DRL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]
2026-05-12 Fix URLs in BOM.csv for better accessibility
    Updated links in BOM.csv to direct URLs, fallout automated checks did not like my old BOM
    [BOM.csv]
2026-05-12 Update BOM.csv to remove formatting characters
    [BOM.csv]
2026-05-12 Fix links for PCB components in README
    Updated links for JLCPCB and LCSC in the Bill of Materials.
2026-05-12 Add LCSC link column to BOM_Board1_PCB1.csv
    [BOM_Board1_PCB1.csv]
2026-05-12 correct 100nF capacitor details in BOM
    copilot hallucinated while trying to appease Fallout AI hallucinations
    [BOM_Board1_PCB1.csv]
2026-05-12 Delete pcb/fabrication/BOM_Board1_PCB1.csv
    This might be tripping up the Fallout AI? I'm grasping at straws here
    [BOM_Board1_PCB1.csv]
2026-05-12 Add supplier part links to BOM
    Updated BOM with supplier part links for components.
2026-05-12 Bill of Materials link issues clarified
    [BOM.csv]
2026-05-12 commas instead of tabs
    [BOM.csv]
2026-05-12 swapped OV2640 part - also a small justification in Overview
    [BOM.csv]

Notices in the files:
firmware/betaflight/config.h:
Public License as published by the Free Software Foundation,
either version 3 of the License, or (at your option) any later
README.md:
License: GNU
